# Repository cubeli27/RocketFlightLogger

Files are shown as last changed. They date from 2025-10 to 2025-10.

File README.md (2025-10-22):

# Rocket Flight Logger

## Overview

**Rocket Flight Logger** is developed for meassuring the acceleration of a pressurised rocket. The intial setup was d1-mini with esp8266 dev board and external IMU and battery connected with soldered wires. This project combines that into one board aiming to reduce all unnecessary weight.  

<p align="center">
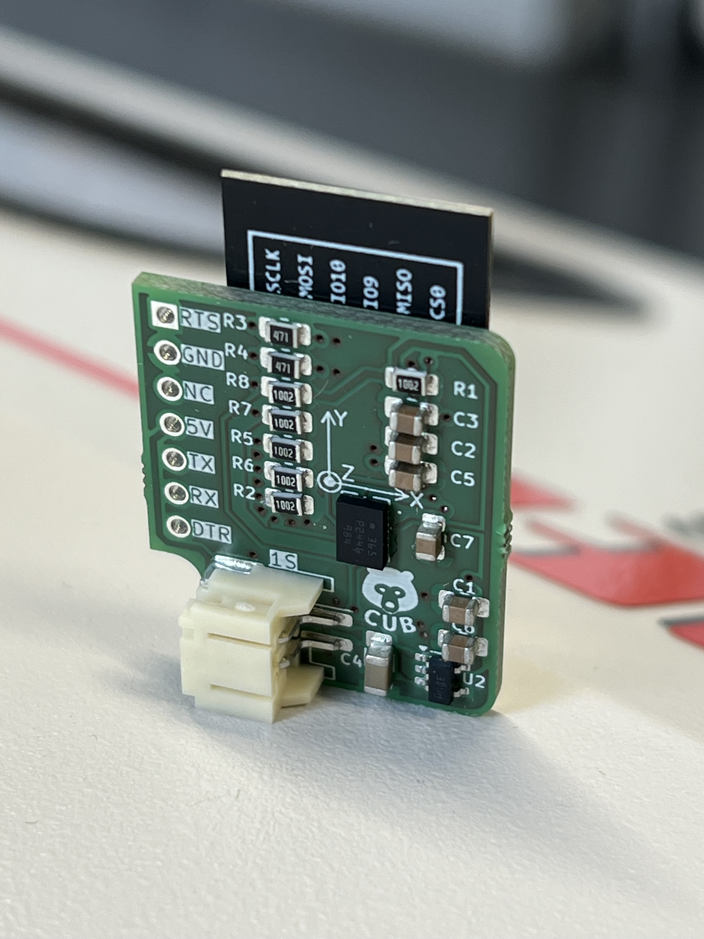
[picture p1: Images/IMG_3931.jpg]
  
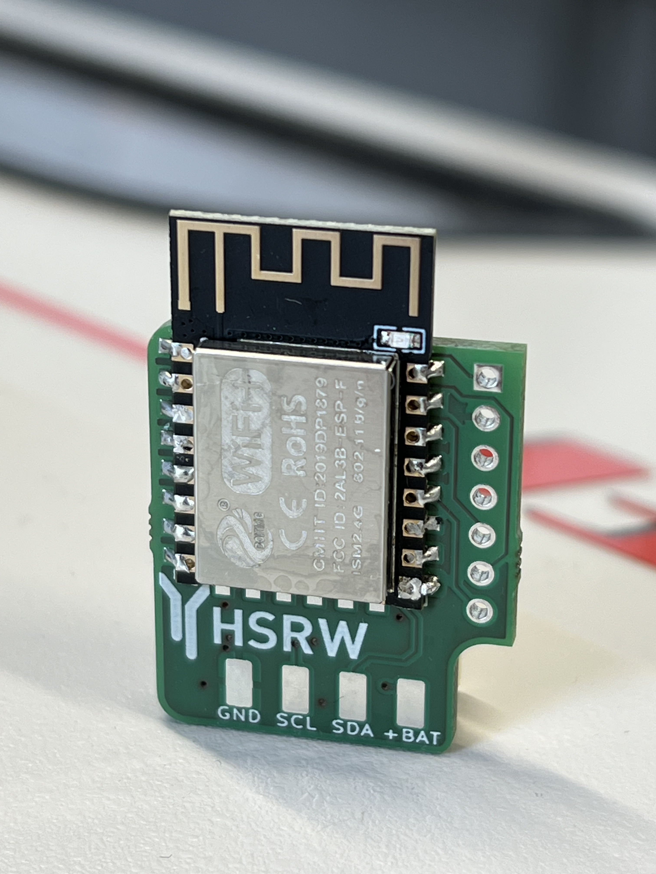
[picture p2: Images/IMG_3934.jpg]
  
</p>

**Key Features:**
- 1S Bat connector on-board
- BMI088 IMU on-board
- Autoboot circuit simplified
- Minimal component count
- Programmer not part of PCBA

---

## Project Structure

| Folder | Description |
|---|---|
| **CAD_files** | Contains `.stl` files  |
| **ECAD_files** | Contains PCB files |
| **Images** | ... |
| **Source_Code** | Firmware developed for this project |

---

## Wiring Diagram

How to program fresh boards.

<p align="center">
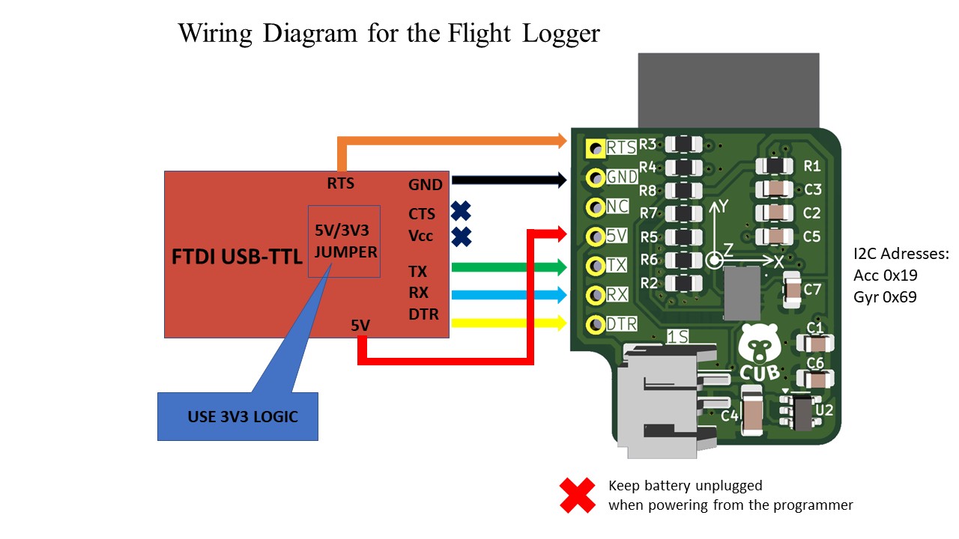
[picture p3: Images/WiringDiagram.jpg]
WiringDiagram
  
</p>

---

## Final Results

PCB on the Rocket (pending)

---
## Future Work

Will be determined after more testing. 

## Author

Developed by **cubeli27**  
For questions or collaboration, feel free to reach out through GitHub.

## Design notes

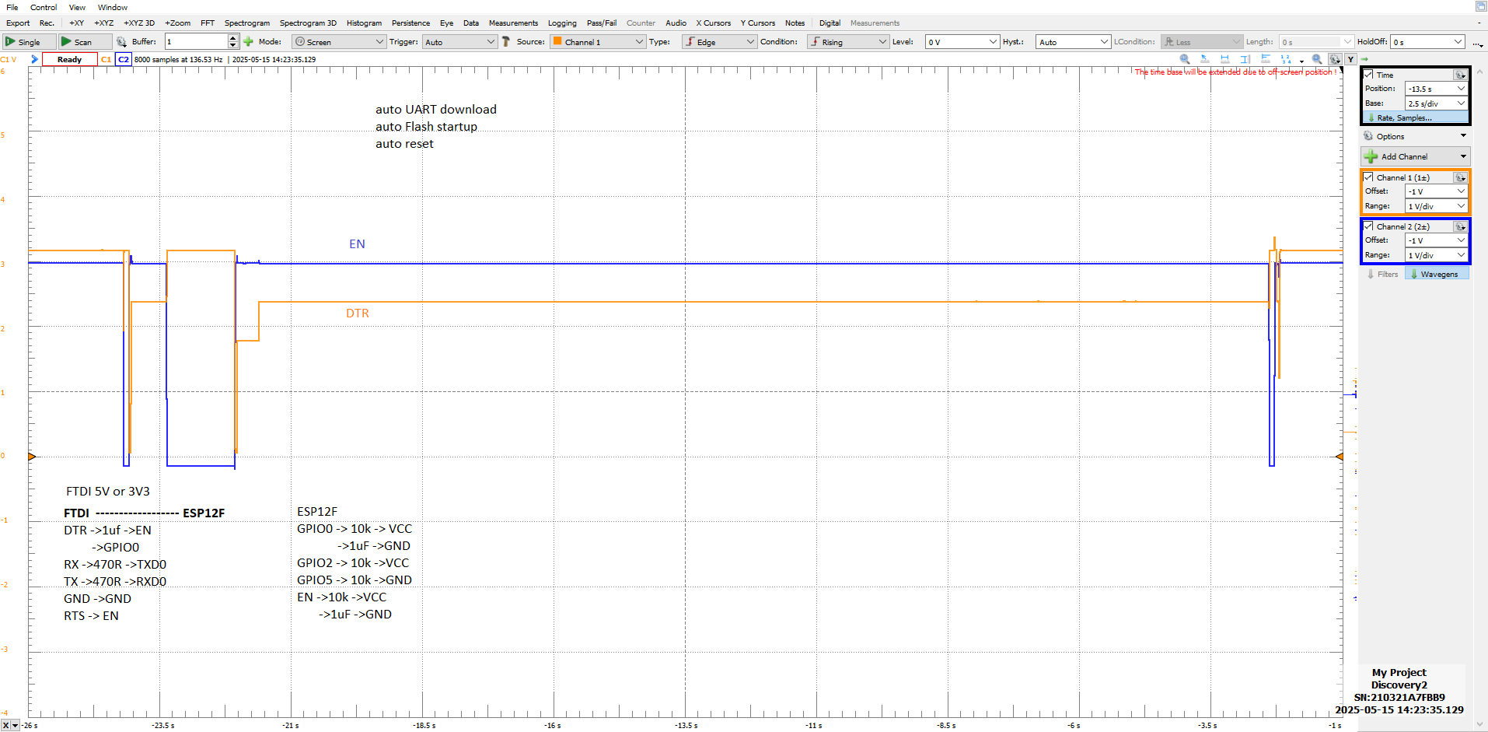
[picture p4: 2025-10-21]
Images/working.png

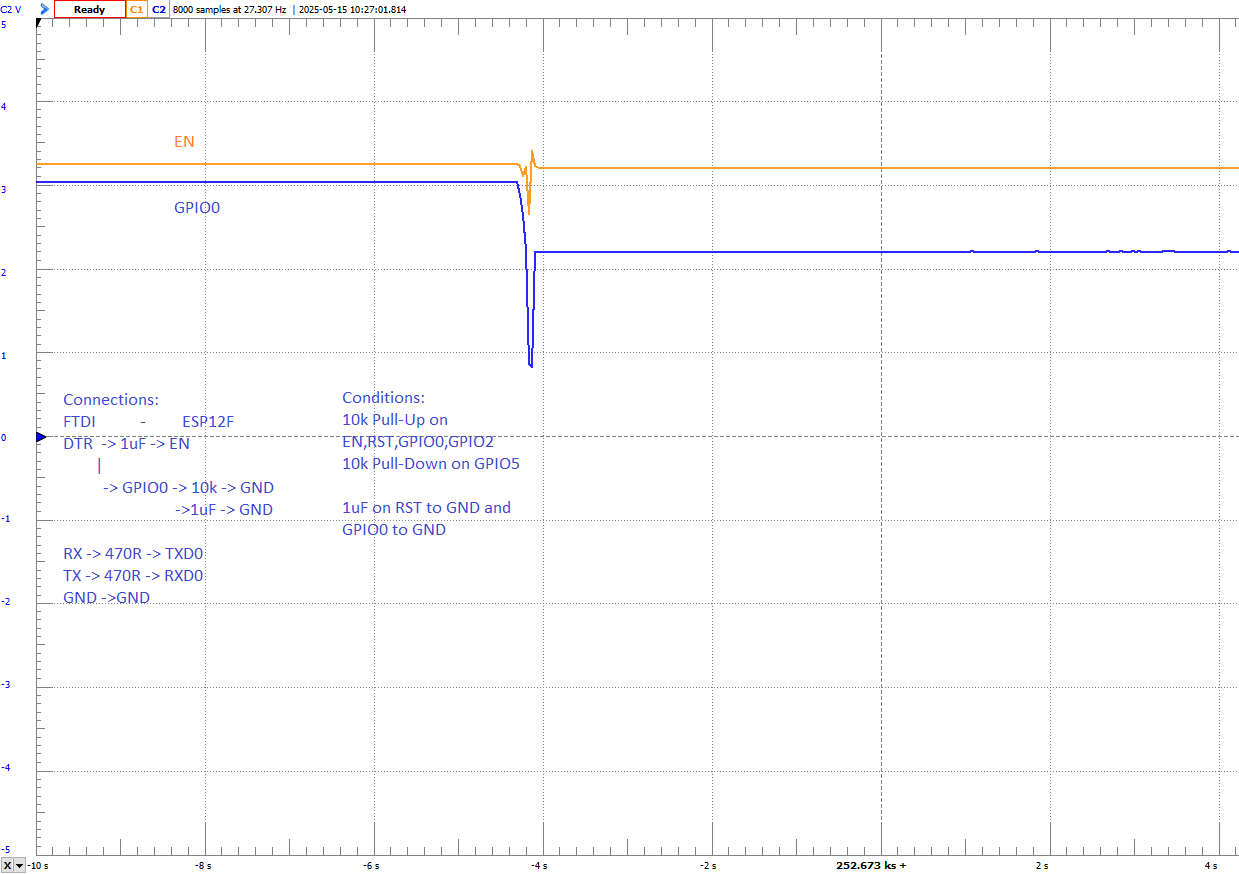
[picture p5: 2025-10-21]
Images/DTRvsEN.png

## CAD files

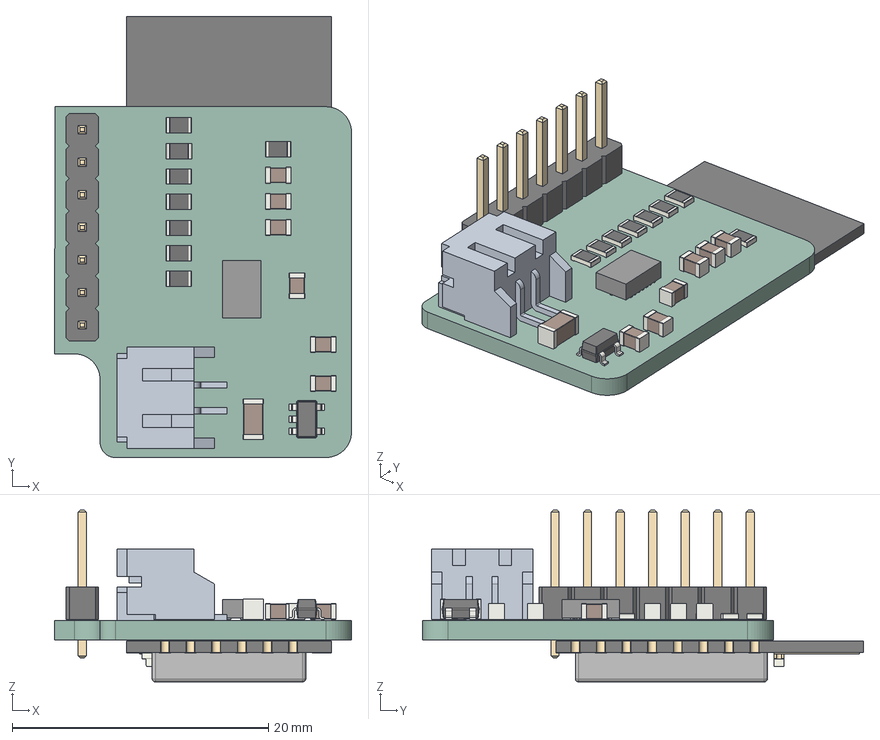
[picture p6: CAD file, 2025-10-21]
CAD_files/RocketFlightLogger.step
23.2 x 34.4 x 13.4 mm
C_0805_2012Metric x 6
R_0805_2012Metric x 8
C_1206_3216Metric
SOT-23-5
PinHeader_1x07_P2.54mm_Vertical
Pins
S2B-PH-SM4-TB_LF__SN_
ESP-12E
RocketFlightLogger_PCB

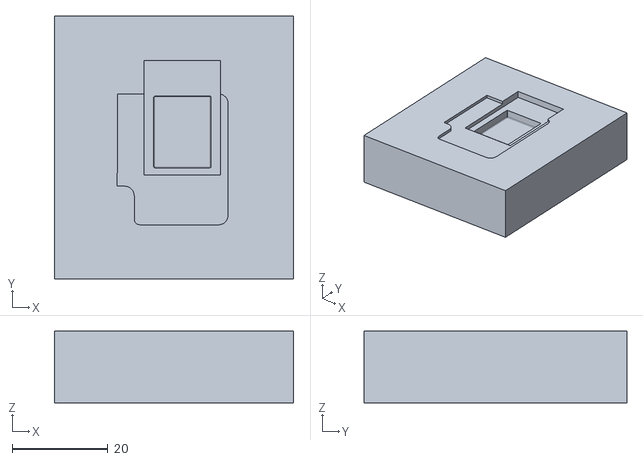
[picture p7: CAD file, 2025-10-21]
CAD_files/FlightLogger-DebugHolder.stl
50.0 x 55.0 x 15.0

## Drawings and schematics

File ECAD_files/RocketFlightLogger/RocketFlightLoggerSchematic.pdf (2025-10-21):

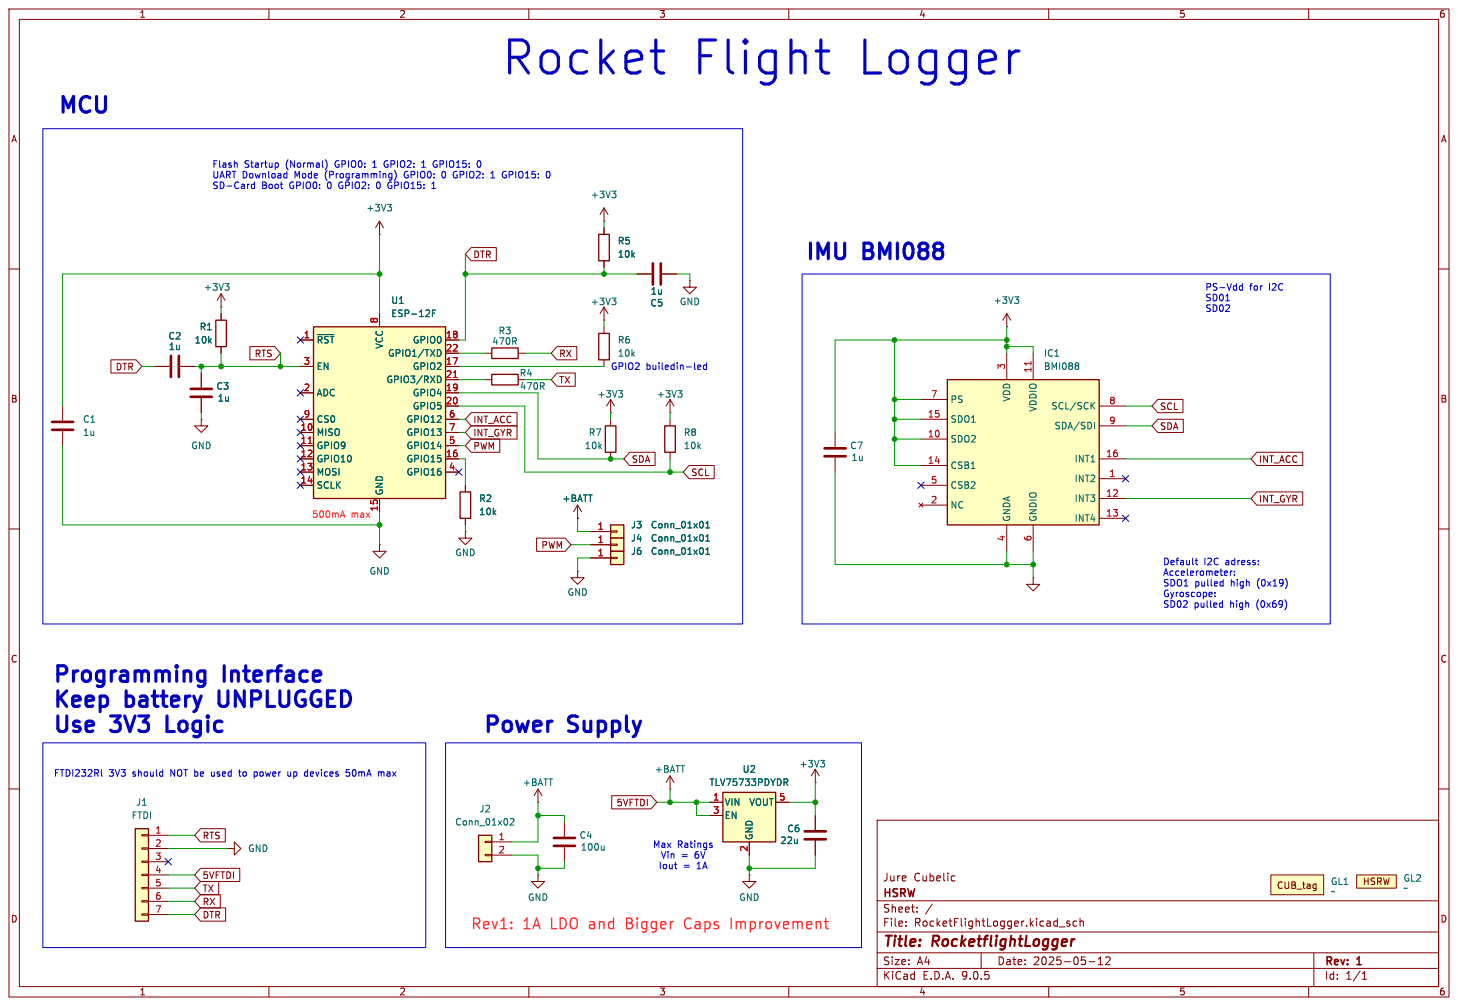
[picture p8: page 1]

8 GND 15 GPIO0 18 GPIO1/TXD 22 GPIO2 17 GPIO3/RXD 21 GPIO4 19 GPIO5 20 GPIO12 6 GPIO13 7 GPIO14 5 GPIO15 16 GPIO16 4 U1ESP-12F GND

GPIO2 builedin-led Rev1: 1A LDO and Bigger Caps Improvement Max Ratings Vin = 6V

6 SCL/SCK 8 SDA/SDI 9

Default I2C adress: Accelerometer: SDO1 pulled high (0x19)

FTDI232Rl 3V3 should NOT be used to power up devices 50mA max

Id: 1/1 Title: RocketflightLogger File: RocketFlightLogger.kicad_sch Sheet: / HSRW

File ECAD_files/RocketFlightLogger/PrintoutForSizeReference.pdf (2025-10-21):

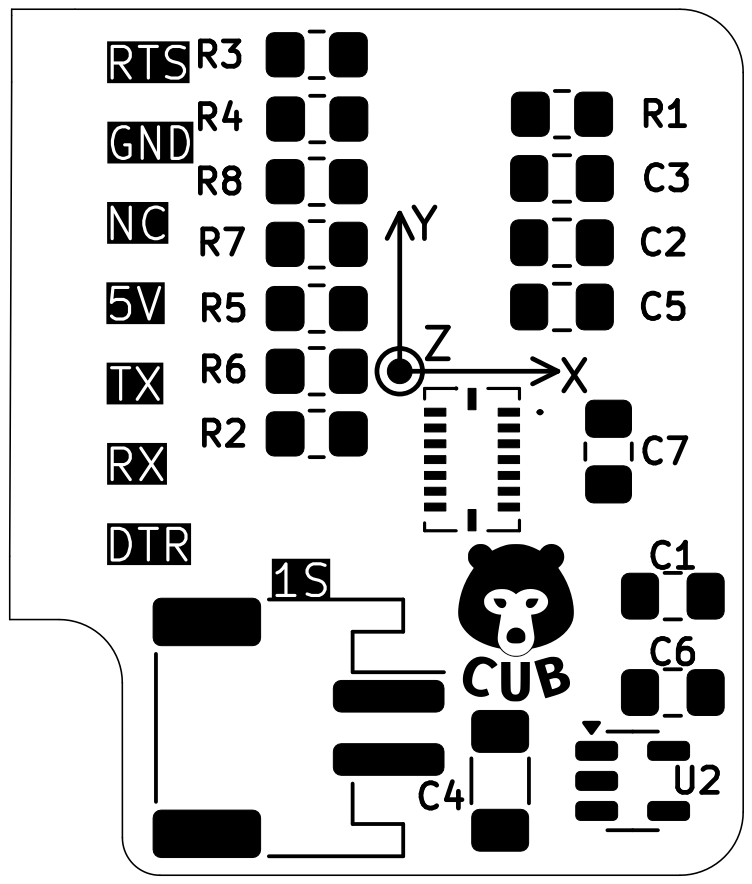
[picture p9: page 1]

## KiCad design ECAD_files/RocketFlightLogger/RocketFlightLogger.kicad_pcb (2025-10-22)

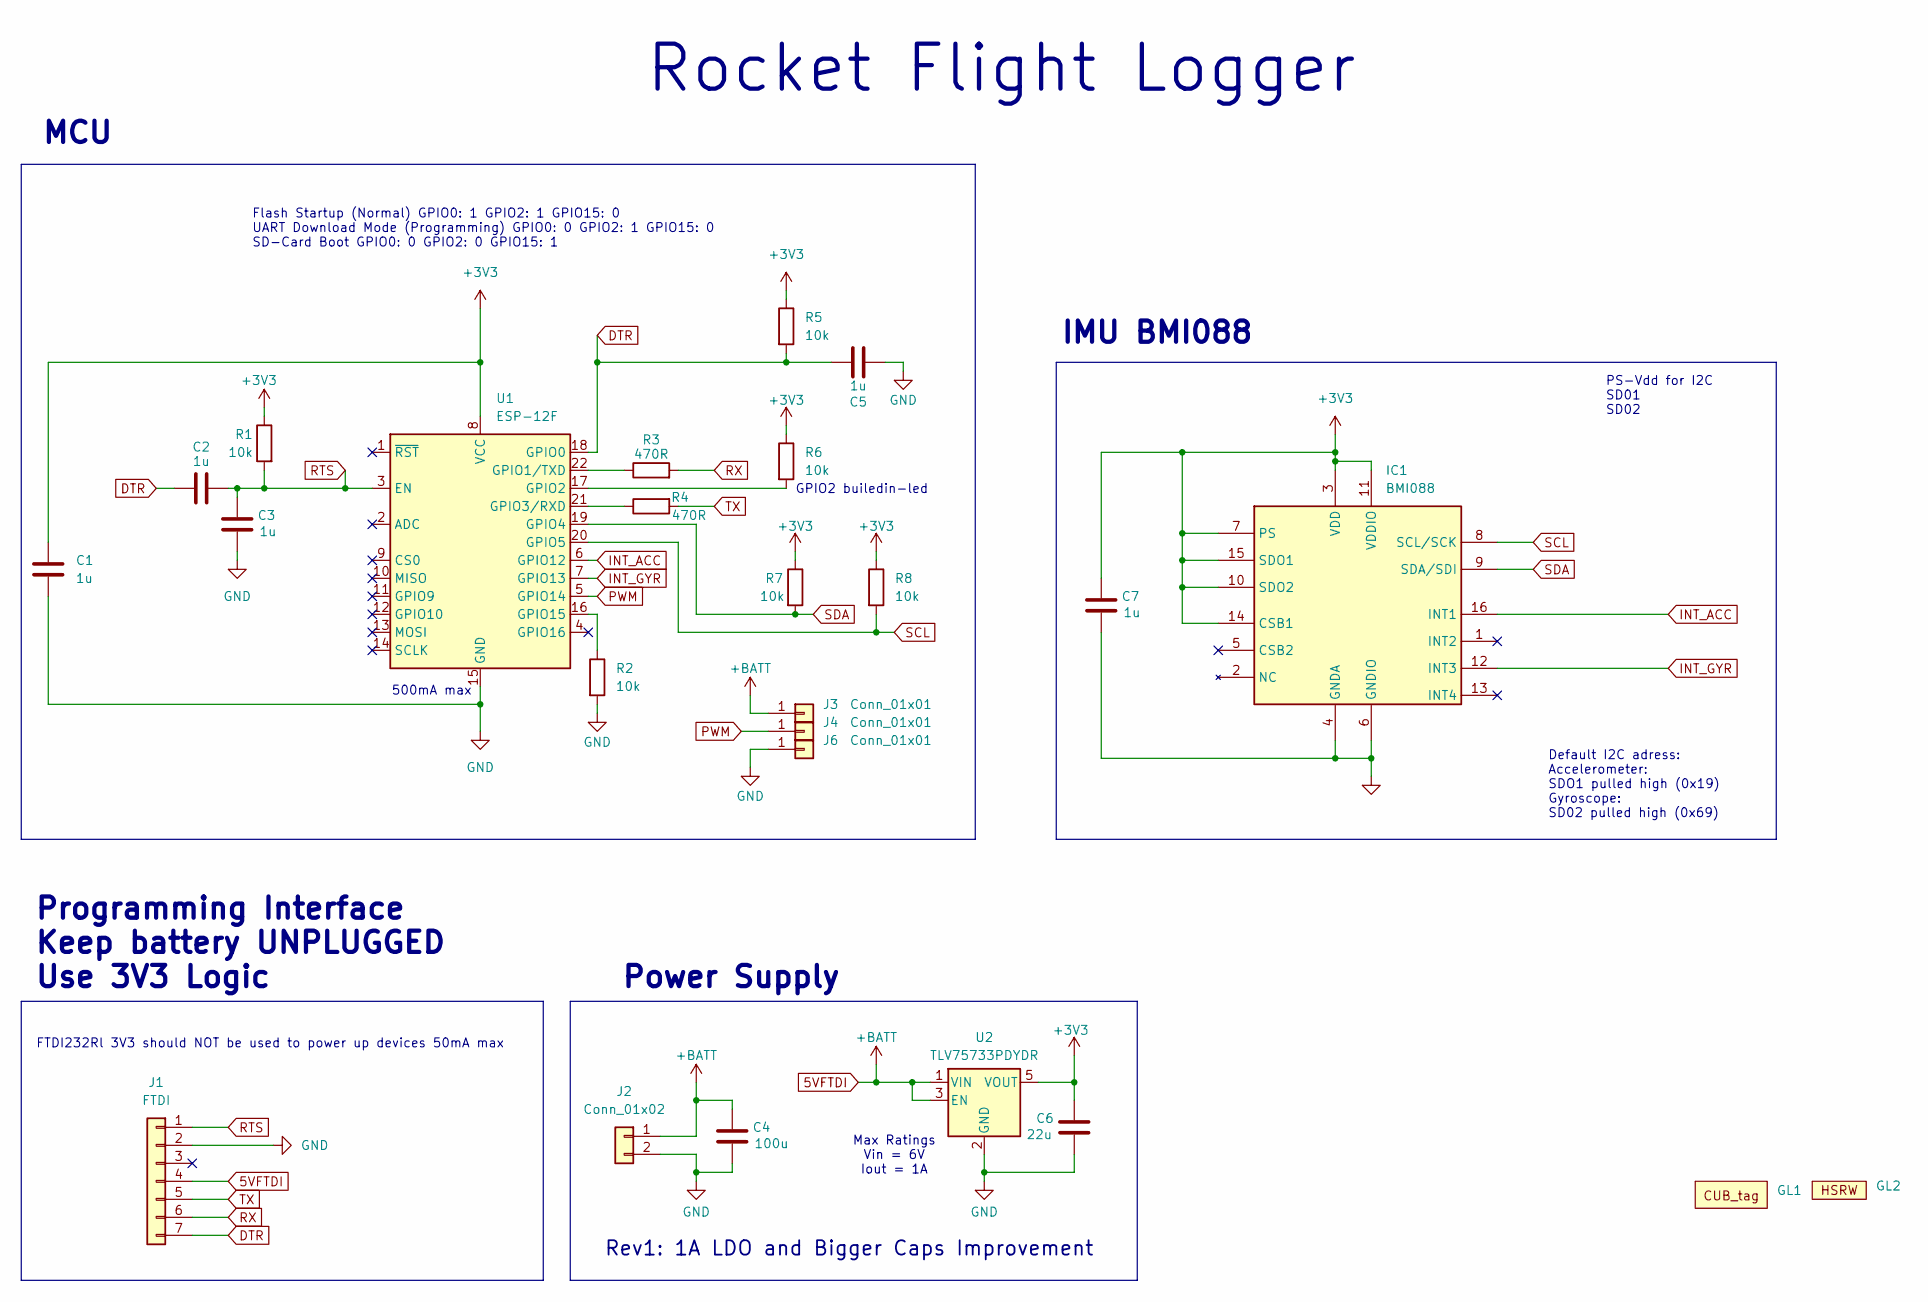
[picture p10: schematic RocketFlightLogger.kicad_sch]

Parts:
C1, C2, C3, C5, C7: 1u; C_0805_2012Metric_Pad1.18x1.45mm_HandSolder
C4: 100u; C_1206_3216Metric_Pad1.33x1.80mm_HandSolder
C6: 22u; C_0805_2012Metric_Pad1.18x1.45mm_HandSolder
GL1: CUB_tag
GL2: hsrwBS
IC1: BMI088; Mouser Part Number 262-BMI088
J1: FTDI; PinHeader_1x07_P2.54mm_Vertical
J2: Conn_01x02; JST_PH_S2B-PH-SM4-TB_1x02-1MP_P2.00mm_Horizontal
J3, J4, J6: Conn_01x01; TestPoint_Keystone_5015_Micro_Mini
R1, R2, R5, R6, R7, R8: 10k; R_0805_2012Metric_Pad1.20x1.40mm_HandSolder
R3, R4: 470R; R_0805_2012Metric_Pad1.20x1.40mm_HandSolder
U1: ESP-12F; ESP-12E
U2: TLV75733PDYDR; SOT-23-5

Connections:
5VFTDI: C4.1, J1.4, J2.1, J3.1, U2.1 (VIN), U2.3 (EN)
+3V3: C1.1, C6.1, C7.1, IC1.3 (VDD), IC1.7 (PS), IC1.10 (SDO2), IC1.11 (VDDIO), IC1.14 (CSB1), IC1.15 (SDO1), R1.1, R5.1, R6.1, R7.1, R8.1, U1.8 (VCC), U2.5 (VOUT)
DTR: C2.1, C5.1, J1.7, R5.2, U1.18 (GPIO0)
GND: C1.2, C3.2, C4.2, C5.2, C6.2, C7.2, IC1.4 (GNDA), IC1.6 (GNDIO), J1.2, J2.2, J6.1, R2.2, U1.15 (GND), U2.2 (GND)
INT_ACC: IC1.16 (INT1), U1.6 (GPIO12)
INT_GYR: IC1.12 (INT3), U1.7 (GPIO13)
unnamed: R3.1, U1.22 (GPIO1/TXD)
unnamed: R6.2, U1.17 (GPIO2)
unnamed: R4.1, U1.21 (GPIO3/RXD)
unnamed: R2.1, U1.16 (GPIO15)
PWM: J4.1, U1.5 (GPIO14)
RTS: C2.2, C3.1, J1.1, R1.2, U1.3 (EN)
RX: J1.6, R3.2
SCL: IC1.8 (SCL/SCK), R8.2, U1.20 (GPIO5)
SDA: IC1.9 (SDA/SDI), R7.2, U1.19 (GPIO4)
TX: J1.5, R4.2

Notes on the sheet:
Programming Interface Keep battery UNPLUGGED Use 3V3 Logic
GPIO2 builedin-led
Flash Startup (Normal) GPIO0: 1 GPIO2: 1 GPIO15: 0 UART Download Mode (Programming) GPIO0: 0 GPIO2: 1 GPIO15: 0 SD-Card Boot GPIO0: 0 GPIO2: 0 GPIO15: 1
Power Supply
PS-Vdd for I2C SD01 SD02
Max Ratings Vin = 6V Iout = 1A
FTDI232Rl 3V3 should NOT be used to power up devices 50mA max
Rev1: 1A LDO and Bigger Caps Improvement
Default I2C adress: Accelerometer: SDO1 pulled high (0x19) Gyroscope: SD02 pulled high (0x69)
MCU
IMU BMI088
500mA max
Rocket Flight Logger

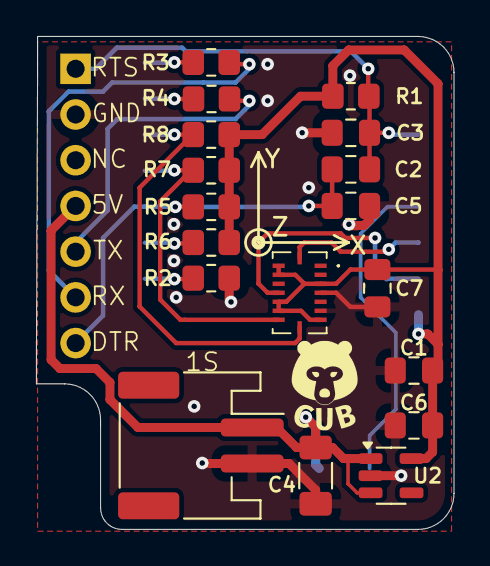
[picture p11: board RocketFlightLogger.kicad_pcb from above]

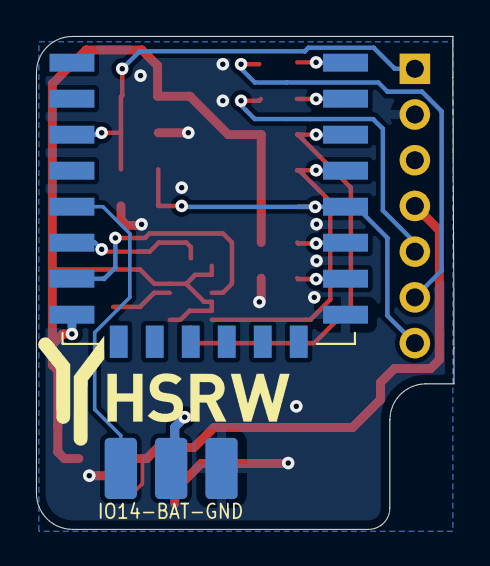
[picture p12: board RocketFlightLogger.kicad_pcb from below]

Board: 2 copper layers, 23.2 x 27.4 mm, 25 parts (4 on the bottom side), 16 nets.

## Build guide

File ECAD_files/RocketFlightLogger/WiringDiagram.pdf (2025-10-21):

## Wiring Diagram for the Flight Logger

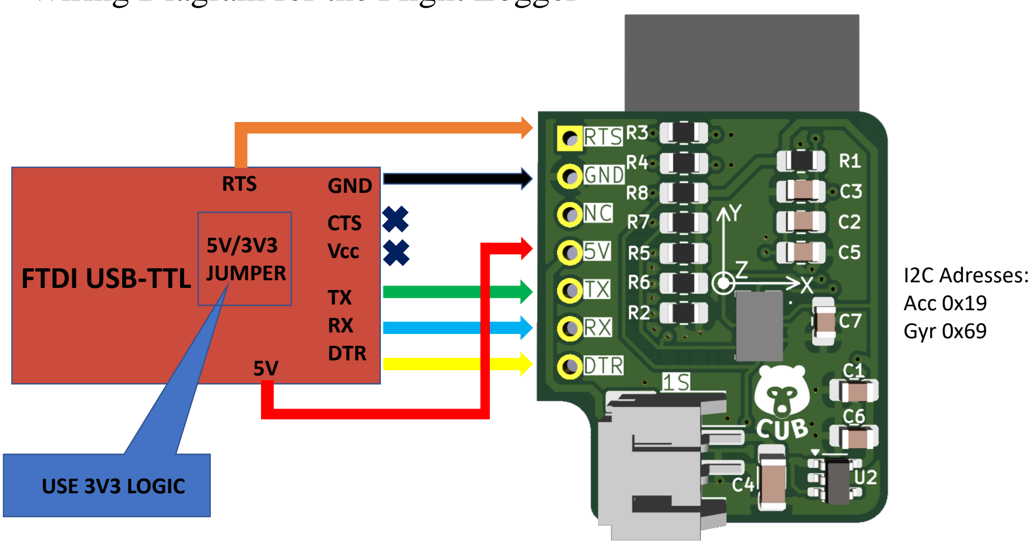
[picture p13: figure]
I2C Adresses: Acc 0x19 Gyr 0x69; USE 3V3 LOGIC; GND; TX RX DTR; RTS; FTDI USB-TTL; CTS; Vcc; JUMPER

Keep battery unplugged
when powering from the programmer

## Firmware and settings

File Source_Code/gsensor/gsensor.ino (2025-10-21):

/*
BSD 3-Clause License

Copyright (c) 2025, Thomas Grunenberg
All rights reserved.

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
1. Redistributions of source code must retain the above copyright notice, this
   list of conditions and the following disclaimer.

2. Redistributions in binary form must reproduce the above copyright notice,
   this list of conditions and the following disclaimer in the documentation
   and/or other materials provided with the distribution.

3. Neither the name of the copyright holder nor the names of its
   contributors may be used to endorse or promote products derived from
   this software without specific prior written permission.

THIS SOFTWARE IS PROVIDED BY THE COPYRIGHT HOLDERS AND CONTRIBUTORS "AS IS"
AND ANY EXPRESS OR IMPLIED WARRANTIES, INCLUDING, BUT NOT LIMITED TO, THE
IMPLIED WARRANTIES OF MERCHANTABILITY AND FITNESS FOR A PARTICULAR PURPOSE ARE
DISCLAIMED. IN NO EVENT SHALL THE COPYRIGHT HOLDER OR CONTRIBUTORS BE LIABLE
FOR ANY DIRECT, INDIRECT, INCIDENTAL, SPECIAL, EXEMPLARY, OR CONSEQUENTIAL
DAMAGES (INCLUDING, BUT NOT LIMITED TO, PROCUREMENT OF SUBSTITUTE GOODS OR
SERVICES; LOSS OF USE, DATA, OR PROFITS; OR BUSINESS INTERRUPTION) HOWEVER
CAUSED AND ON ANY THEORY OF LIABILITY, WHETHER IN CONTRACT, STRICT LIABILITY,
OR TORT (INCLUDING NEGLIGENCE OR OTHERWISE) ARISING IN ANY WAY OUT OF THE USE
OF THIS SOFTWARE, EVEN IF ADVISED OF THE POSSIBILITY OF SUCH DAMAGE.
*/

#include "BMI088.h"

#include <ESP8266WiFi.h>
#include <ESP8266WebServer.h>
#include <ESP8266mDNS.h>

// For Device ID
#include <EEPROM.h>

// For Time/Date
#include <TimeLib.h>

/*
Size of Pre recorded Data-Sets (must be smaller than 255)
*/
#define PREDATALOG_SIZE 100

/*
Size of Recorded Data-Sets (do not use too much memory....)
*/
#define DATALOG_SIZE 1800


/*
Threshold value for autostart (total of x+y+z accalaration)
*/
#define AUTOSTART_VALUE 25

/* accel object */
Bmi088Accel accel(Wire,0x19);
/* gyro object */
Bmi088Gyro gyro(Wire,0x69);



// WLAN Zugangsdaten. Bitte hier ein ordentliches Passwort auswählen.
const char *ssid = "gsensor";
const char *password = "1234567890";
const char* hostname = "esp";


ESP8266WebServer server(80);

/**********************************************************/
// Global Memory 
/**********************************************************/
bool printmode = false;
unsigned char deviceID;


/**********************************************************/
// Global Memory for data logging
/**********************************************************/
struct logdata_t {
	signed short x;
	signed short y;
  signed short z;
};

logdata_t* accprelog = NULL;
logdata_t* gyroprelog = NULL;

logdata_t* acclog = NULL;
logdata_t* gyrolog = NULL;

volatile int16_t logpos = -1;
volatile int8_t prelogpos = 0;

volatile bool autostart = true;

// Recoring starting time
int recordstart_year;
int recordstart_month;
int recordstart_day;
int recordstart_hour;
int recordstart_minute;
int recordstart_second;




//--------------------------------------------------------------------------------------------------------------------------------
// ISR
// Interrupt runs 100 times per second (100Hz)
void ICACHE_RAM_ATTR onTimer() {
 
  // Update sensor data ..................................................................
 
  // read the accel
  accel.readSensor();

  // read the gyro
  gyro.readSensor();

  // Data logging ........................................................................
  
  // Start log on event if autostart is enabled
  if ( (logpos < 0) && (abs(accel.getAccelX_mss()) + abs(accel.getAccelY_mss()) + abs(accel.getAccelZ_mss()) > AUTOSTART_VALUE) && autostart ){
    logpos = 0;
    recordstart_year = year();
    recordstart_month = month();
    recordstart_day = day();
    recordstart_hour = hour();
    recordstart_minute = minute();
    recordstart_second = second();
  }
  
  // Log data until the memory is full
  if ( (logpos > -1) && (logpos < DATALOG_SIZE) ){
    acclog[logpos].x = accel.getAccelX_mss() * 100;
    acclog[logpos].y = accel.getAccelY_mss() * 100; 
    acclog[logpos].z = accel.getAccelZ_mss() * 100;
    gyrolog[logpos].x = gyro.getGyroX_rads() * 100;
    gyrolog[logpos].y = gyro.getGyroY_rads() * 100;
    gyrolog[logpos].z = gyro.getGyroZ_rads() * 100;

    logpos++;
  }

  // Before logging save pre data
  if ( logpos < 0 ){
    accprelog[prelogpos].x = accel.getAccelX_mss() * 100;
    accprelog[prelogpos].y = accel.getAccelY_mss() * 100;
    accprelog[prelogpos].z = accel.getAccelZ_mss() * 100;
    gyroprelog[prelogpos].x = gyro.getGyroX_rads() * 100;
    gyroprelog[prelogpos].y = gyro.getGyroY_rads() * 100;
    gyroprelog[prelogpos].z = gyro.getGyroZ_rads() * 100;
    if (++prelogpos >= PREDATALOG_SIZE)
      prelogpos = 0;
  }
}
//--------------------------------------------------------------------------------------------------------------------------------




void handleRoot() {
  String html = "<html><body>";
  html += "<form id=\"timeForm\" action=\"/settime\" method=\"GET\">";
  html += "Stunde: <input type=\"number\" id=\"hour\" name=\"hour\" min=\"0\" max=\"23\"><br>";
  html += "Minute: <input type=\"number\" id=\"minute\" name=\"minute\" min=\"0\" max=\"59\"><br>";
  html += "Sekunde: <input type=\"number\" id=\"second\" name=\"second\" min=\"0\" max=\"59\"><br>";
  html += "Tag: <input type=\"number\" id=\"day\" name=\"day\" min=\"1\" max=\"31\"><br>";
  html += "Monat: <input type=\"number\" id=\"month\" name=\"month\" min=\"1\" max=\"12\"><br>";
  html += "Jahr: <input type=\"number\" id=\"year\" name=\"year\" min=\"2020\" max=\"2100\"><br>";
  html += "<input type=\"submit\" value=\"Set Time\">";
  html += "</form>";

  // JavaScript zur automatischen Uhrzeiteingabe
  html += "<script>";
  html += "const now = new Date();";
  html += "document.getElementById('hour').value = now.getHours();";
  html += "document.getElementById('minute').value = now.getMinutes();";
  html += "document.getElementById('second').value = now.getSeconds();";
  html += "document.getElementById('day').value = now.getDate();";
  html += "document.getElementById('month').value = now.getMonth() + 1;";
  html += "document.getElementById('year').value = now.getFullYear();";
  html += "document.getElementById('timeForm').submit();";
  html += "</script>";

  html += "</body></html>";
  server.send(200, "text/html", html);
}


void handleSetTime() {
  if (server.hasArg("hour") && server.hasArg("minute") && server.hasArg("second") &&
      server.hasArg("day") && server.hasArg("month") && server.hasArg("year")) {
    
    int currentHour = server.arg("hour").toInt();
    int currentMinute = server.arg("minute").toInt();
    int currentSecond = server.arg("second").toInt();
    int currentDay = server.arg("day").toInt();
    int currentMonth = server.arg("month").toInt();
    int currentYear = server.arg("year").toInt();


    // Uhrzeit setzen
    setTime(currentHour, currentMinute, currentSecond, currentDay, currentMonth, currentYear);
    Serial.printf("Timeset to: %02d:%02d:%02d am %02d.%02d.%d\n", 
                  currentHour, currentMinute, currentSecond, 
                  currentDay, currentMonth, currentYear);
  }
  
  String answer = "<html>\n";
  answer += "<head>\n";
  answer += "<meta http-equiv=\"refresh\" content=\"1; url=/ui\">\n";
  answer += "</head></body>\n";
  answer += "<h3>Zeit gesetzt</h3>";
  answer += "</body></html>\n"; 

  server.send(200, "text/html", answer);
}

void handleUI(){
  String answer = "<html>\n";
  answer += "<head>\n";
  answer += "<title>MPU 6050 Beschleunigungssensor</title>\n";
  answer += "<meta http-equiv=\"refresh\" content=\"2\" >\n";
  
  if (logpos < 0){
    if (autostart){
      answer += "</head><body bgcolor=green><h2>Data logger ready</h2>\n";
      answer += "<a href=\"/autostartoff\"><button>Autostart deaktivieren</button></a>\n";
    } else {
      answer += "</head><body bgcolor=white><h2>Data logger stopped</h2>\n";  
      answer += "<a href=\"/autostarton\"><button>Autostart aktivieren</button></a>\n";
    }

  } else {
    if (logpos < DATALOG_SIZE){
      answer += "</head><body bgcolor=red><h2>Recording data</h2>\n";
      answer +=  "<progress value=\"" + String(logpos) + "\" max=\"" + String(DATALOG_SIZE) + "\"></progress>";
    } else {
      answer += "</head><body bgcolor=blue><h2>Data recorded</h2>\n";
      answer += "<p>";
      answer += "<a href=\"/download\" download><button>Download data</button></a>\n";
      answer += "<a href=\"/reset\" onclick=\"return confirm('Are you sure?');\"><button>Reset data</button></a>\n";
      answer += "</p><p>";
    }
  }

  answer += "<h2>Beschleunigungen:</h2>\n";
  answer += "<h3>X-Achse: " + String(accel.getAccelX_mss()) + "</h3>\n";
  answer += "<h3>Y-Achse: " + String(accel.getAccelY_mss()) + "</h3>\n";   
  answer += "<h3>Z-Achse: " + String(accel.getAccelZ_mss()) + "</h3>\n";
  answer += "<h2>Gyroskop:</h2>\n";
  answer += "<h3>X-Achse: " + String(gyro.getGyroX_rads()) + "</h3>\n";
  answer += "<h3>Y-Achse: " + String(gyro.getGyroY_rads()) + "</h3>\n";   
  answer += "<h3>Z-Achse: " + String(gyro.getGyroZ_rads()) + "</h3>\n"; 
  answer += "<h3>Temperatur: " + String(accel.getTemperature_C()) + "&deg;C</h3>\n"; 
  answer += "<br/>";
  answer += "<h1>Aktuelle Uhrzeit:</h1>";
  answer += "<p><h2>" + String(hour()) + ":" + String(minute()) + ":" + String(second()) + "</h2></p>";
  answer += "<a href=\"/\" Set Time><button>Set Time</button></a>\n"; 
  answer += "<h1>Device ID:</h1>";
  answer += "<p><h2>" + String(deviceID) + "</h2></p>";
  answer += "</p></body>";

  server.send(200, "text/html", answer);
}


void resetlogdata(){

  // Reset data logging
  logpos = -1;
  autostart = false;

  // Create Answer
  String answer = "<html>\n";
  answer += "<head>\n";
  answer += "<title>Reset log data</title>\n";
  answer += "<meta http-equiv=\"refresh\" content=\"2; url=/ui\">\n";
  answer += "</head><body>\n";
  answer += "<h1>Reset log data</h1>\n";
  answer += "</body>"; 

  server.send(200, "text/html", answer);
}


void downloadlogdata(){
  uint16_t i;

  // Prevent execution when datalog is not complete
  if (logpos != DATALOG_SIZE)
    return;

  // Stop Sensor and Datalog Interrupt
   timer1_disable();
  
  // Creating filename
  String filename = "gSensor";
  char tmp[10];
  snprintf(tmp, 8, "%03d", deviceID);
  filename += tmp;
  filename += "_";
  snprintf(tmp, 4, "%04d", recordstart_year);
  filename += tmp;
  snprintf(tmp, 4, "%02d", recordstart_month);
  filename += tmp;
  snprintf(tmp, 4, "%02d", recordstart_day);
  filename += tmp;
  filename += "_"; 
  snprintf(tmp, 4, "%02d", recordstart_hour);
  filename += tmp;
  snprintf(tmp, 4, "%02d", recordstart_minute);
  filename += tmp;
  snprintf(tmp, 4, "%02d", recordstart_second);
  filename += tmp; 

  String webPageFirstLine = "Index;AccX;AccY;AccZ;GyroX;GyroY;GyroZ\n";
  server.setContentLength(CONTENT_LENGTH_UNKNOWN);
  server.sendHeader("Content-Disposition", "attachment; filename=" + filename + ".txt");
  server.send(200, "text/plain", webPageFirstLine);
  
  // Pre Recorded data
  for (i = 0; i < PREDATALOG_SIZE; i++) {
    String csvline = String(i - PREDATALOG_SIZE);
    csvline += ";";
    csvline += String(accprelog[((i + prelogpos) % PREDATALOG_SIZE)].x/100.0);
    csvline += ";";
    csvline += String(accprelog[((i + prelogpos) % PREDATALOG_SIZE)].y/100.0);
    csvline += ";";
    csvline += String(accprelog[((i + prelogpos) % PREDATALOG_SIZE)].z/100.0);
    csvline += ";";
    csvline += String(gyroprelog[((i + prelogpos) % PREDATALOG_SIZE)].x/100.0);
    csvline += ";";
    csvline += String(gyroprelog[((i + prelogpos) % PREDATALOG_SIZE)].y/100.0);
    csvline += ";";
    csvline += String(gyroprelog[((i + prelogpos) % PREDATALOG_SIZE)].z/100.0);    
    csvline += "\n";
    server.sendContent(csvline);
  }

  // Recorded data
  for (i = 0; i < DATALOG_SIZE; i++) {
    
    String csvline = String(i);
    csvline += ";";
    csvline += String((acclog[i].x)/100.0);
    csvline += ";";
    csvline += String((acclog[i].y)/100.0);
    csvline += ";";
    csvline += String((acclog[i].z)/100.0);
    csvline += ";";
    csvline += String((gyrolog[i].x)/100.0);
    csvline += ";";
    csvline += String((gyrolog[i].y)/100.0);
    csvline += ";";
    csvline += String((gyrolog[i].z)/100.0);
    csvline += "\n";
    server.sendContent(csvline);
  }

  // End of Data
  server.sendContent("");


  // Re-Enable Timer1 interrupt
  timer1_isr_init();
  timer1_attachInterrupt(onTimer);
  timer1_enable(TIM_DIV16, TIM_EDGE, TIM_LOOP);
  timer1_write(50000); // Timer auf 10ms setzen
}


void autostarton(){

  // Reset data logging
  autostart = true;

  // Create Answer
  String answer = "<html>\n";
  answer += "<head>\n";
  answer += "<title>Autostart</title>\n";
  answer += "<meta http-equiv=\"refresh\" content=\"2; url=/ui\">\n";
  answer += "</head><body>\n";
  answer += "<h1>Autostart aktiv</h1>\n";
  answer += "</body>"; 

  server.send(200, "text/html", answer);
}

void autostartoff(){

  // Reset data logging
  autostart = false;

  // Create Answer
  String answer = "<html>\n";
  answer += "<head>\n";
  answer += "<title>Autostart</title>\n";
  answer += "<meta http-equiv=\"refresh\" content=\"2; url=/ui\">\n";
  answer += "</head><body>\n";
  answer += "<h1>Autostart deaktiviert</h1>\n";
  answer += "</body>"; 

  server.send(200, "text/html", answer);
}


void setup(void) {
  int status;

  // Onboard LED
  pinMode(LED_BUILTIN, OUTPUT);
  digitalWrite(LED_BUILTIN, HIGH);  // Turn the LED off by making the voltage HIGH

  // Serial output
  Serial.begin(115200);
  while (!Serial) {
    delay(10); // will pause Zero, Leonardo, etc until serial console opens
  }

  // Malloc memory for data logging
  accprelog = new logdata_t[PREDATALOG_SIZE];
  gyroprelog = new logdata_t[PREDATALOG_SIZE];

  acclog = new logdata_t[DATALOG_SIZE];
  gyrolog = new logdata_t[DATALOG_SIZE];

  if ( (accprelog == NULL) || (acclog == NULL)){
    Serial.println("Memoy alloc failed!");
    while(1){
      digitalWrite(LED_BUILTIN, LOW);
      delay(300);
      digitalWrite(LED_BUILTIN, HIGH);
      delay(300);   
    }
  }

  // Device ID
  EEPROM.begin(1);
  deviceID = EEPROM.read(0);

  // Try to initialize!
  accel.setRange(Bmi088Accel::RANGE_24G);
  accel.setOdr(Bmi088Accel::ODR_1600HZ_BW_234HZ);
  status = accel.begin();

  if (status < 0) {
    Serial.println("Accel Initialization Error");
    Serial.println(status);
    while (1) { // Fast flash blue LED
      digitalWrite(LED_BUILTIN, LOW);
      delay(100);
      digitalWrite(LED_BUILTIN, HIGH);
      delay(100);
    }
  }
  gyro.setOdr(Bmi088Gyro::ODR_2000HZ_BW_230HZ);
  gyro.setRange(Bmi088Gyro::RANGE_1000DPS);  
  status = gyro.begin();
  if (status < 0) {
    Serial.println("Gyro Initialization Error");
    Serial.println(status);
    while (1) { // Fast flash blue LED
      digitalWrite(LED_BUILTIN, LOW);
      delay(100);
      digitalWrite(LED_BUILTIN, HIGH);
      delay(100);
    }
  }

  Serial.println("Starte Access Point...");
  WiFi.setOutputPower(10); // reduce transmit power to 10mW
  
  // Adapt WiFi-SSID to device ID
  String myssid = ssid;
  myssid += String((int)deviceID);
  WiFi.softAP(myssid.c_str(), password);

  // IP Adresse anzeigen (sollte 192.168.4.1 sein)
  IPAddress myIP = WiFi.softAPIP();
  Serial.print("AP IP address: ");
  Serial.println(myIP);

  // Server einrichten und starten. Es wird hier nur die
  // Seite "/" (Hauptseite) angelegt. Die Funktion handleRoot
  // ist oben angelegt. So etwas nennt sich Callback Funktion.
  server.on("/", handleRoot);

  server.on("/reset", resetlogdata);
  server.on("/download", downloadlogdata);
  server.on("/autostarton", autostarton);
  server.on("/autostartoff", autostartoff);

  server.on("/ui", handleUI);
  server.on("/settime", handleSetTime);


  server.begin();
  Serial.println("HTTP server started");

  // Start mDNS responder
  if (MDNS.begin(hostname)) {
    Serial.print("mDNS responder started with hostname: ");
    Serial.println(hostname);
    MDNS.addService("http", "tcp", 80); // Add a service (optional)
  }

  Serial.println("");


  // Short flash the blue LED
  digitalWrite(LED_BUILTIN, LOW);
  delay(600);
  digitalWrite(LED_BUILTIN, HIGH);

  // Timer initialisieren
  timer1_isr_init();
  timer1_attachInterrupt(onTimer);
  timer1_enable(TIM_DIV16, TIM_EDGE, TIM_LOOP);
  timer1_write(50000); // Timer auf 10ms setzen
}


void loop() {

  MDNS.update();
  server.handleClient();  // Web server access

  // Show with blue onboard LED that logger is ready
  if (logpos < 0 && autostart)
    digitalWrite(LED_BUILTIN, LOW);
  else
    digitalWrite(LED_BUILTIN, HIGH);


  // Print out the values
  if (printmode){
    Serial.print(accel.getAccelX_mss());
    Serial.print("\t");
    Serial.print(accel.getAccelY_mss());
    Serial.print("\t");
    Serial.print(accel.getAccelZ_mss());
    Serial.print("\t");
    Serial.print(gyro.getGyroX_rads());
    Serial.print("\t");
    Serial.print(gyro.getGyroY_rads());
    Serial.print("\t");
    Serial.print(gyro.getGyroZ_rads());
    Serial.print("\t");
    Serial.print(accel.getTemperature_C());
    Serial.print("°C,"); 
    Serial.print("Logpos:");
    Serial.print(logpos);
    Serial.println("");
  }


  // Process serial commands
  if (Serial.available() > 0) {
    String command = Serial.readStringUntil('\n');
    command.trim();

    // Check if command is a number
    bool isNumber = true;
    for (int i = 0; i < command.length(); i++) {
      if (!isDigit(command.charAt(i))) {
        isNumber = false; // Zeichen ist keine Ziffer
        break;
      }
    }
    if (isNumber)
      Serial.print("Got number: ");
    else
      Serial.print("Got command: ");
    Serial.println(command);

    // Ganzzahl => Device ID 
    if (isNumber) {
      int num = command.toInt();
      if (num > 0 && num < 255){
      deviceID = num;
      Serial.print("Set device ID to: ");
      Serial.println(deviceID);
      EEPROM.write(0, deviceID);
      EEPROM.commit();
      }
    }

    // Printmode
    if (!isNumber && command.equalsIgnoreCase("print") ){
      printmode = !printmode;
    }

     // Info
    if (!isNumber && command.equalsIgnoreCase("info") ){
      Serial.print("Device ID: ");
      Serial.println(deviceID); 
      Serial.printf("Time: %02d:%02d:%02d am %02d.%02d.%d\n", 
                  hour(), minute(), second(), day(), month(), year());
      Serial.print("Free RAM: ");
      Serial.print( ESP.getMaxFreeBlockSize() );
      Serial.println(" bytes");

      Serial.print("accprelog: ");
      Serial.println((int)accprelog,HEX);
      Serial.print("gyroprelog: ");
      Serial.println((int)gyroprelog,HEX);
      Serial.print("acclog: ");
      Serial.println((int)acclog,HEX);
      Serial.print("gyrolog: ");
      Serial.println((int)gyrolog,HEX);

    }
  }
}
